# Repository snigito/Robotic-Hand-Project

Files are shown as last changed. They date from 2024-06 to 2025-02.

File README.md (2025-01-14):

# Origin of the project 

The genesis of this independent project was when I was approached by the head of my high school to see if I could make a robotic hand to be “Thing” in our school’s spring musical, the Addams Family. Having a decent knowledge of robotics, computer science and electrical work from working on the robotics team and making other projects, this was an interesting challenge for me. I began to research online and found that there were no commercially made hands and no hands that could be rented. The best robotic hand I saw online was made as a promotion for the Netflix series Wednesday, but it took a professional special effects studio with a team of six people five months to make it. 

After researching different options, I decided to make a robotic hand that would mirror my own hand movements while wearing a glove equipped with sensors. I found someone online who had made an arduino flex-sensor controlled robotic hand. The youtube video I used for inspiration can be found [here](https://www.youtube.com/watch?v=Fvg-v8FPcjg)

# Core Materials

Arduinos are small programmable computers that are cheap and easy to use for small projects like this one. Initially I was using a regular ESP-32, but because they do not have a screen or a battery, it would not have been possible to make Thing wireless. I decided to use the Heltec WiFi LoRa 32 (V3) because it is smaller than a regular Arduino (1” x 0.5”), it has a USB C charging port, a rechargeable battery, WiFi, Bluetooth, and an LED screen. 

<div align="center">
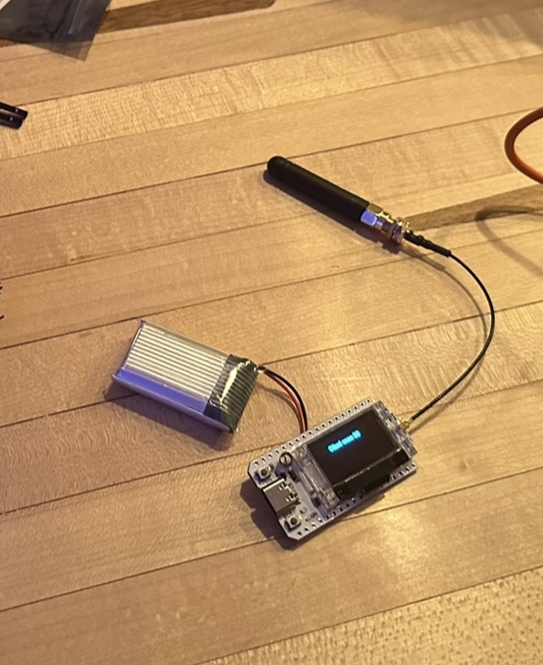
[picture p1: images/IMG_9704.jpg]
Picture of Arduino
  
</div>

The second core component of this project are the flex resistors which are long strips that increase resistance as they are bent. They have little electrical resistance (ohms) when they are straight, but the more they are flexed, the greater the resistance. 

<div align="center">
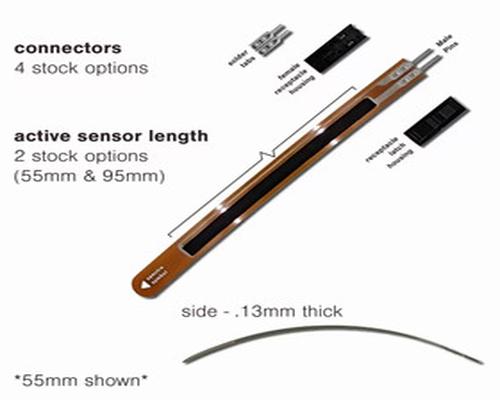
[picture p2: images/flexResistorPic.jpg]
Picture of Flex resistor
  
</div>

The store page to buy these is [here](https://www.spectrasymbol.com/resistive-flex-sensors)

Another important component are the servos, a great staple of any electronics project.

<div align="center">
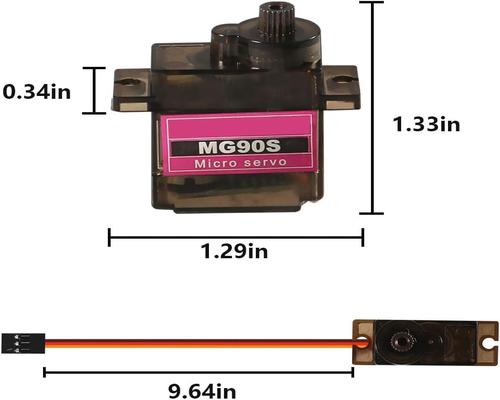
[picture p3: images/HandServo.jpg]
Picture of Servo
  
</div>

These servos can be bought [here](https://tinyurl.com/rhu3s3ph)

The servos I used are very small motors that can turn 180 degrees. I needed them to be small because the idea was that they would fit inside the hand eventually, and I wanted the hand to be a normal size. Servos interface easily with Arduino, and they are easy to code. I used five servos, one for each finger. 

# General Design of the Hand 

The design shown in the above video has a good base, but had a lot of issues I wanted to resolve in my final design. Notably, it used a wired connection meaning that it would not be able to move far from the person controlling it. As a proof of concept this is perfectly fine, but for the play I wanted Thing to be wireless in order to move from one side of the stage to the other seamlessly. To make this possible I planned to use two Arduinos to communicate with each other over WIFI.

To start prototyping the servo movement code with the Arduinos, I got a small robotic hand with servos from amazon. This hand was much too small to use as a final product but it was good to use for testing.  

<div align="center">
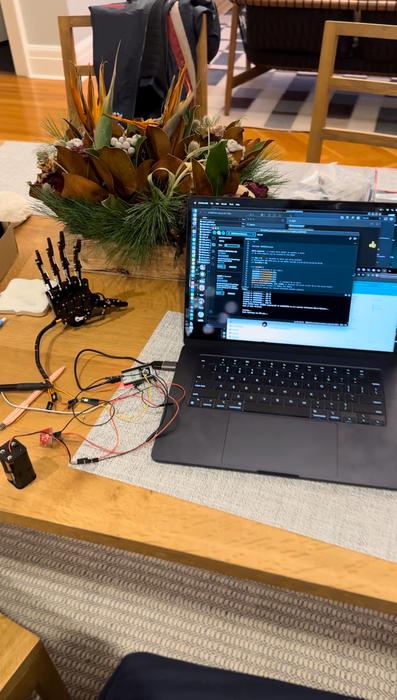
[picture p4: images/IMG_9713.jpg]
Picture of Prototype
  
</div>

Servo motors have a set range of motion (0 to 180). In the code, I put the value that I was setting the servo to in a loop. I started testing the servos by incrementing them and checking both extremes. **VIDEO OF SERVO SWEEP TESTS**

Then I learned about how the WIFI communication system worked between the two Arduinos and repeated the same test. One of the Ardinuos is sending the desired angles to the other one which forwards those commands to the servo and sends it to the desired position. 

Next I made a basic PCB (printed circuit board) so that I could test multiple servos at once in a more streamlined fashion. Each servo needs three wires to function: the power IN (red), the ground which completes the circuit (black), and the signal wire which tells the servo what angle to be at (yellow). In order to make the PCB, I first planned out the routes that I needed the wires to make, counted the pins that I needed going in, and measured the distances of the wires and cut them accordingly. I soldered the wires to the board, made the connections between the (little circles on the board), and used a multimeter to check that each wire was running to where it was supposed to. In the picture below, the top row of pins all go to the servos (5 servos means 15 pins). All of the wires connect to the pins in a sequence: yellow, red, black, yellow, red, black…). In the bottom left, the signal wires go into a ribbon cable connection which connects to the Arduino so that it can control each servo. I had to crimp a female connection onto the ends of the ribbon cable so that it would connect to the male pins on the arduino. The arduino is able to differentiate each servo by the pin number that it is connected to. In the bottom right, the two pins are connected to a small battery pack of AA batteries that provides both the power and ground for the circuit.

<div align="center">
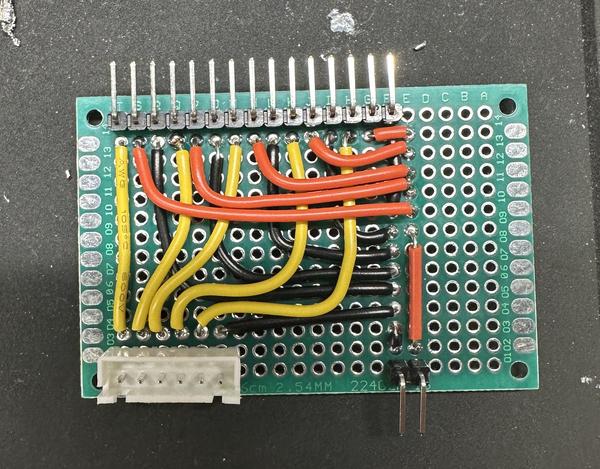
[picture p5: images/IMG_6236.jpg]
Image of Circut Board
  
</div>

<div align="center">
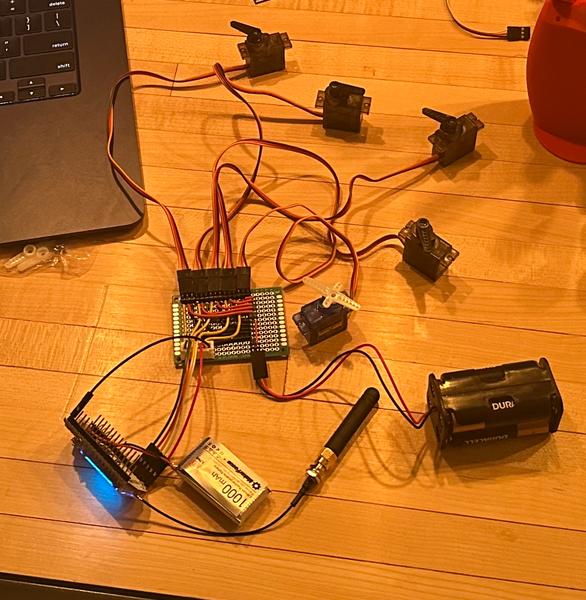
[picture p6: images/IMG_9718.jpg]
Image of Board and Servos
  
</div>

The hand itself and the fingers are all very similar to what was used in the previously mentioned Youtube video. Each finger is separated into three segments (with the thumb being only two segments). Each segment has three holes in it (two of which are larger than the third) and an elastic string is threaded through the holes to hold the fingers together. The elastic string ties off at the tip of each finger and the knuckle at the base of the finger. The elastic string is what is holding the hand together and what keeps the hand upright when the servos are in their “up” position. The tension of the elastic is also what brings the fingers of the hand back up when the servos release to their “up” position. The smaller hole is used for dental floss (fishing line was tried but found to be too stretchy and smooth which resulted in the line detaching from the servos) which connects at the tip of each finger, runs down the inside of the finger through to the palm. The floss is then tied to the servos so that when a servo moves downwards, it will pull on the floss and therefore pull the corresponding finger down. 

<div align="center">
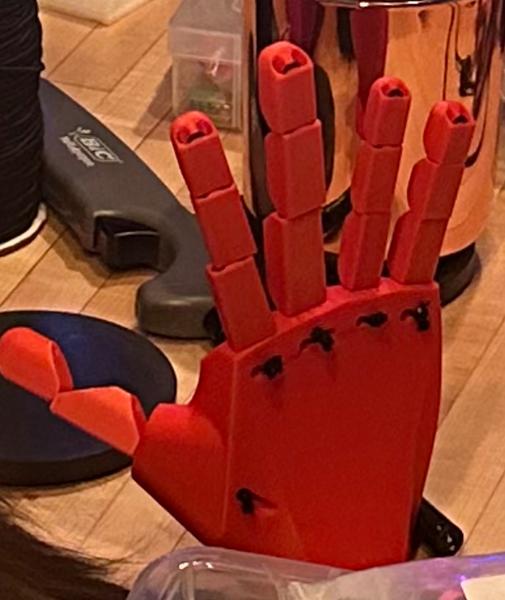
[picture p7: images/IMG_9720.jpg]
Picture of Red Hand 1
  
</div>

<div align="center">
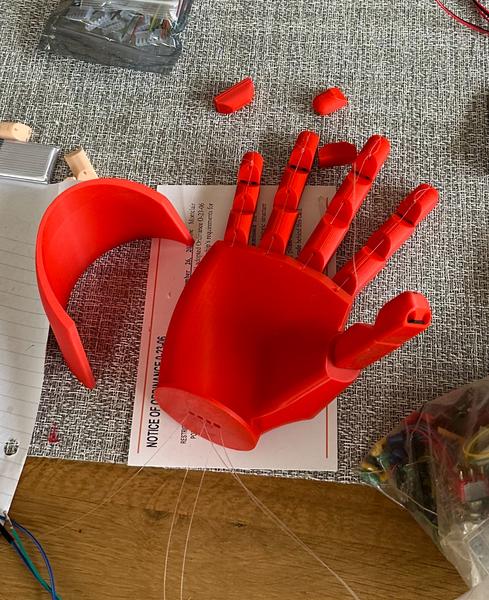
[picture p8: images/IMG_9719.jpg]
Picture of Red Hand 2
  
</div>

These photos show an early prototype 3D printed hand. On the left you see the fishing wire running through and out the bottom of the hand. On the right you can see the black elastic string running through and tied off at the base of the fingers.

The next steps were to figure out a way to mount the servos inside the wrist portion of the hand. The servos needed to fit in a way where their movement arcs would not intersect with one another. In the video I used for inspiration the person doing the project decided to glue the servos to the 3D print but I did not like the idea of that so I decided to make something more permanent. I used metal inserts that can be pressed into the 3D print which allowed me to screw the servos down. I used a special tip for the hot soldering iron to melt the plastic and press the insert into it.

<div align="center">
  Image of First Hand Servo Layout
</div>

<div align="center">
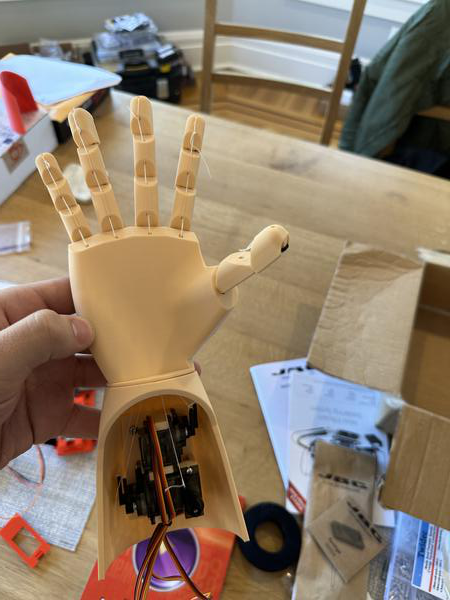
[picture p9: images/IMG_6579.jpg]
Image of Final Hand Servo layout
  
</div>

I changed over to a skin tone color for the 3D print. On the left is an initial servo layout that I tested, but ultimately decided that it did not fit well. 

In order to make the Arduino, circuit board, servo motors, and batteries fit inside the casing I made a new circuit board and changed the layout of the battery pack. The new circuit board had connections so that the Arduino could plug in to the board directly with no wires in between. The battery pack I changed to a flat one where 4 AA batteries are laid parallel to one another and then recessed into the bottom of the housing. This allows for easy access to change out the batteries, adds weight to the bottom to prevent tipping, and is compact so it does not get in the way of other parts. Additionally, there is a small, rechargeable LIPO battery that powers the arduino. The larger battery pack powers the servos in conjunction with the smaller one to make the system work. For ease of use I also added a switch for the power battery wires. It is a DPDT switch with one throw wired in to cut off or allow the flow of power without having to take off the casing to turn it on. I also added a thumbscrew to the casing with a threaded insert to easily access the interior of the hand. I implemented a similar design with the back plate that the servos screw into so that the whole layout could be removed for easy access and servicing. 

<div align="center">
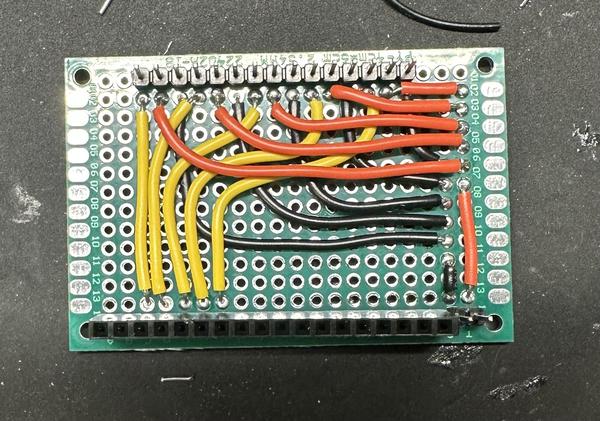
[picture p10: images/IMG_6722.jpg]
Circut Board Picture
  
</div>

<div align="center">
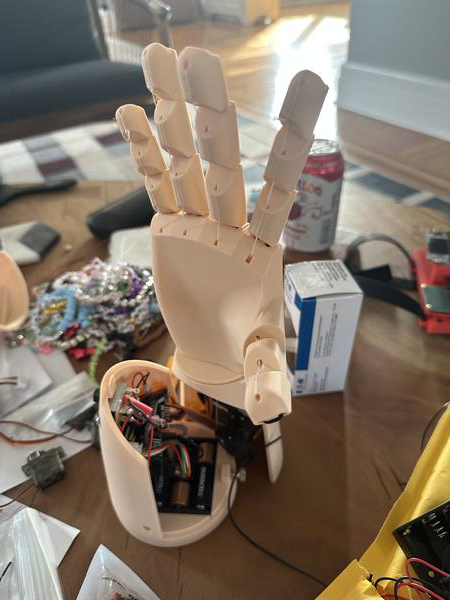
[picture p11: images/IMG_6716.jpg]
Picture of Hand Assembly
  
</div>

The new board shown on the left is functionally the same as the previous one but without the ribbon cable connection so as to cut down on space. The image on the right shows the recessed battery pack, silver thumb screw on the left and the power switch on the top left above the Arduino.

The ranges of the values of the flex resistors were too large  so I used a voltage divider to help balance it out. The signal wires are reading from the voltage after the resistor. 

<div align="center">
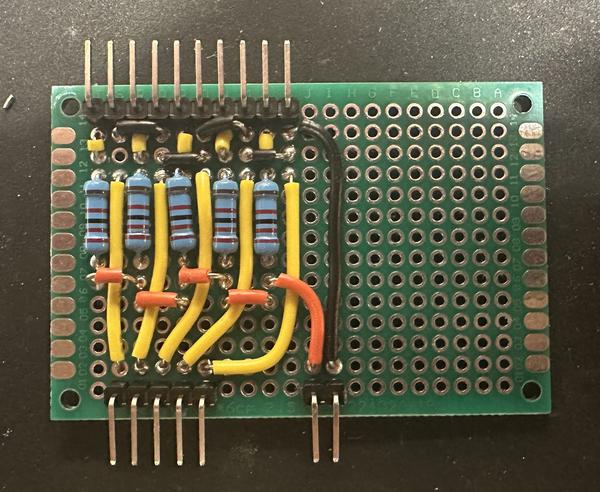
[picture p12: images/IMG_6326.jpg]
Voltage Divider Circut Picture
  
</div>

I designed an arm piece that would strap to my arm using velcro and would hold an arduino and a battery. It could then read the resistance values from each flex resistor and then send it to the other arduino inside the hand. The arduino in the hand then uses these values to move the servos and make the fingers match how mine are moving in the glove. 

<div align="center">
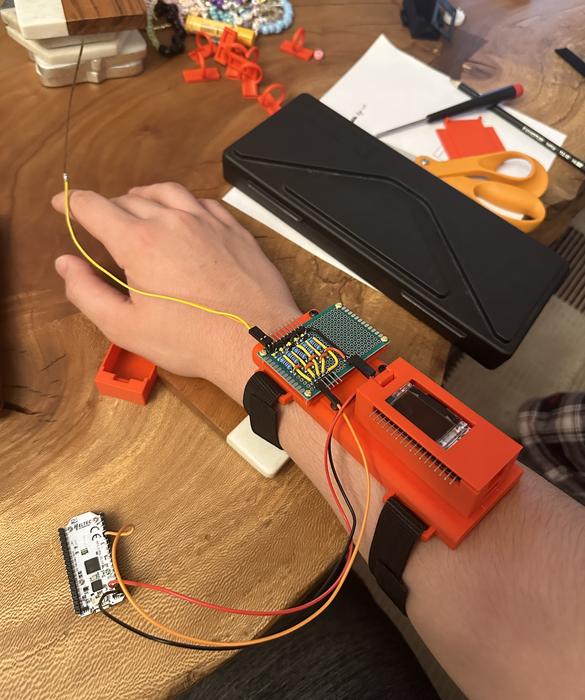
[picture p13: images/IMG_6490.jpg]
Arm Piece Picture
  
</div>

I bought an outdoor work glove and 3D printed guide rails for the flex resistors so that they would stay in a uniform position on each of my fingers. I sewed these guide rails into the outdoor work glove. I also sewed the base of each flex resistor to the base of each finger on the glove. After a few days of play rehearsals which was heavy testing for the glove and the hand, I noticed that the flex resistors values would no longer reflect the originals that we set. I had to hold my fingers and the resistors at awkward angles just to get to the original positions. Sometimes, even that would not work. After some research online, it became clear to me that the resistors’ degradation was a known problem. Therefore, I decided to make a new glove, and on this new one I would sew down the base of each resistor much more than I had on the first glove. 

<div align="center">
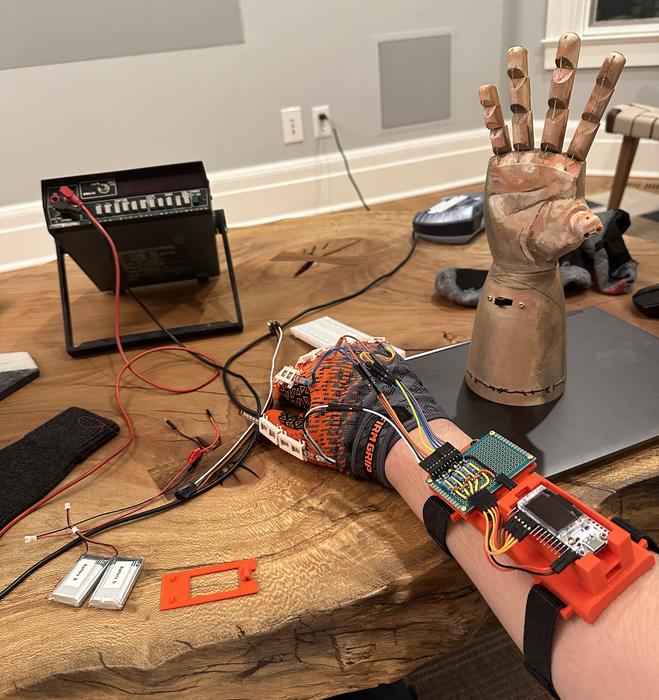
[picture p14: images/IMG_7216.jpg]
Full Glove Picture
  
</div>

All of the programming files can be found below and are fully commented. When running the hand, first I plugged in the battery for the glove arduino, and it starts to look for a specific WIFI network with a specific name and would try the password that we gave it. The Arduino in the hand acts as a WIFI network and the one in the glove works as a WIFI client. This allows the two devices to communicate and send messages to one another. In this case I am using the glove Arduino to record the values of the flex resistors then scale those values to a number between 0 and 180 relative to the resistor’s minimum and maximum. The glove Ardunio then takes that number and the resistor number and sends the hand Ardunio a message in this format: “[resistor number] [desired angle]”. The resistor number corresponds to the servo controlling the same finger which the hand Ardunio sets to the desired angle after receiving the message. Both Arduinos display the values and the resistor number on their OLED screens in a scrolling format. The next value is displayed at the bottom and the preceding ones are shifted up to help with debugging to ensure all the values are expected as well as all the resistors are responsive. The code for this can be found in the text scrolls file. The code for the hand can be found in the 5 servo access point file. The code for the glove is found in the 5 servo client file.

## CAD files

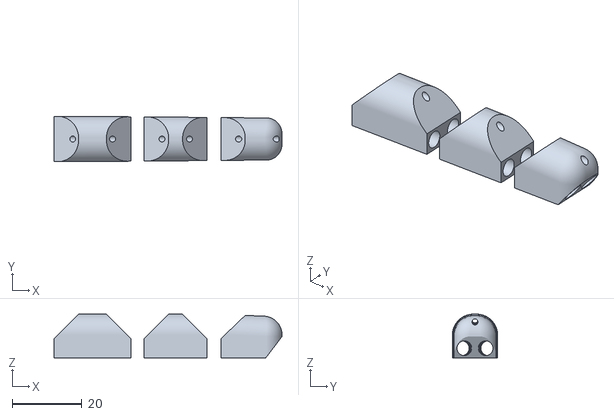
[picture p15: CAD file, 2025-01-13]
Hand Parts/finger_pinky.stl
65.2 x 13.0 x 12.5

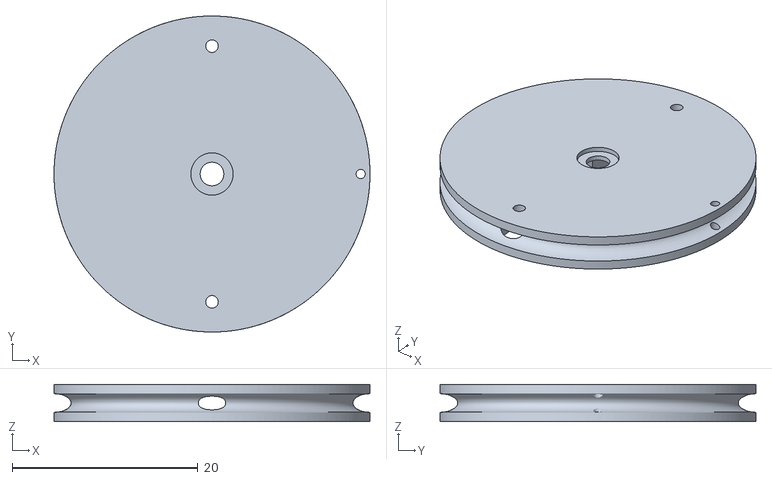
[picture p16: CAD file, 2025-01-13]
Hand Parts/large_servo_horn.stl
34.0 x 34.0 x 4.00

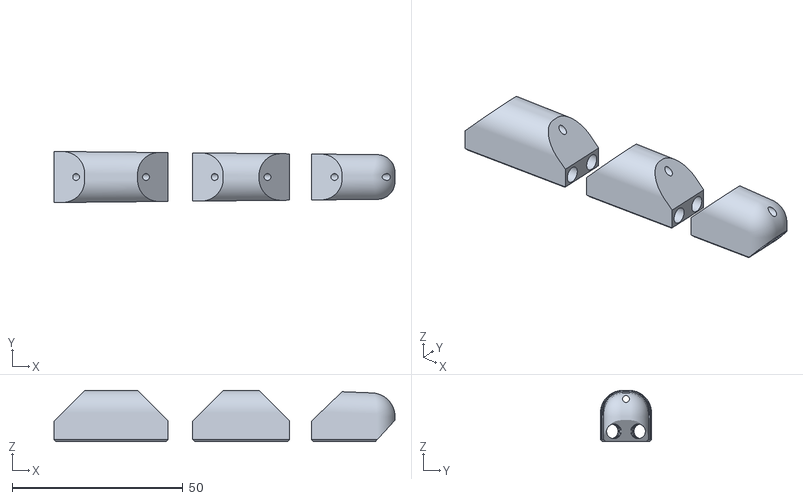
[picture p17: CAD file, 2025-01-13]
Hand Parts/finger_middle.stl
100.0 x 15.0 x 15.0

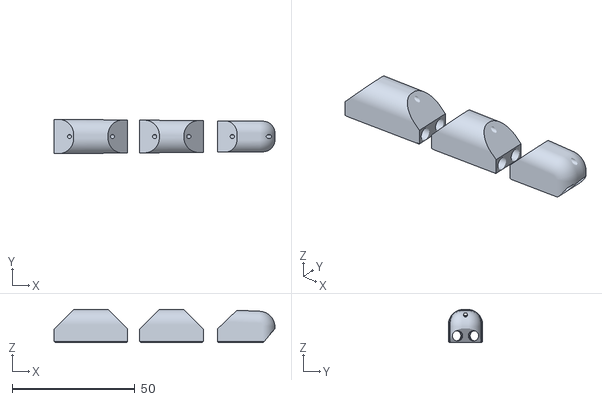
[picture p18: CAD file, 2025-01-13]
Hand Parts/finger_ring.stl
90.0 x 14.0 x 13.5

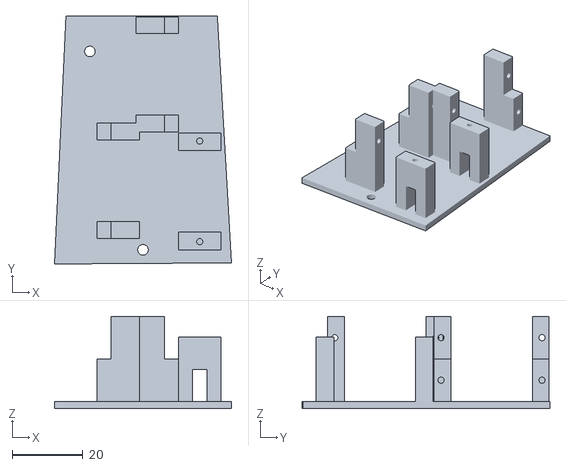
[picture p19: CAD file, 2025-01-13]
Hand Parts/stacked_servo_mount.stl
50.0 x 70.0 x 26.0

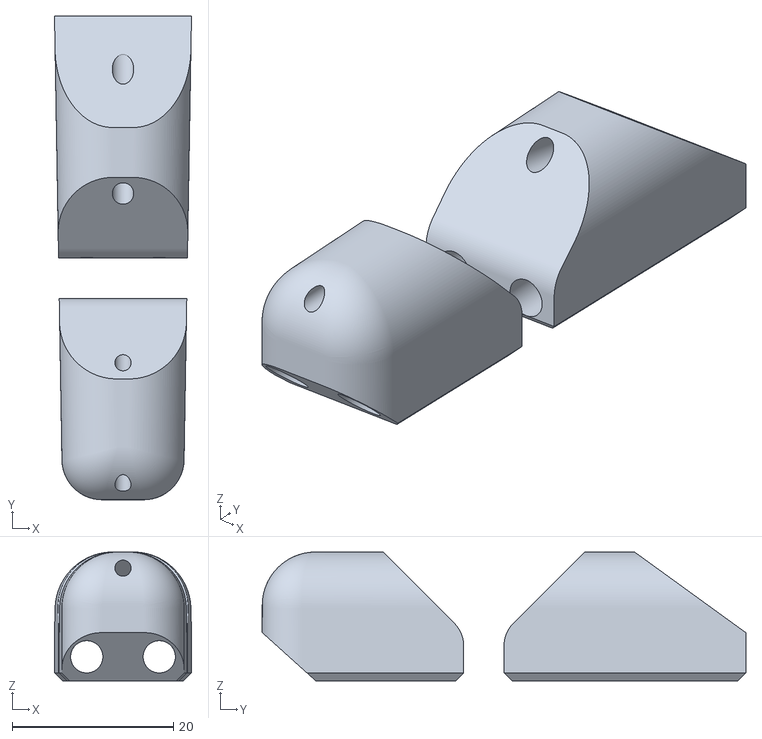
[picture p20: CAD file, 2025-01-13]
Hand Parts/finger_thumb.stl
17.0 x 60.0 x 16.0

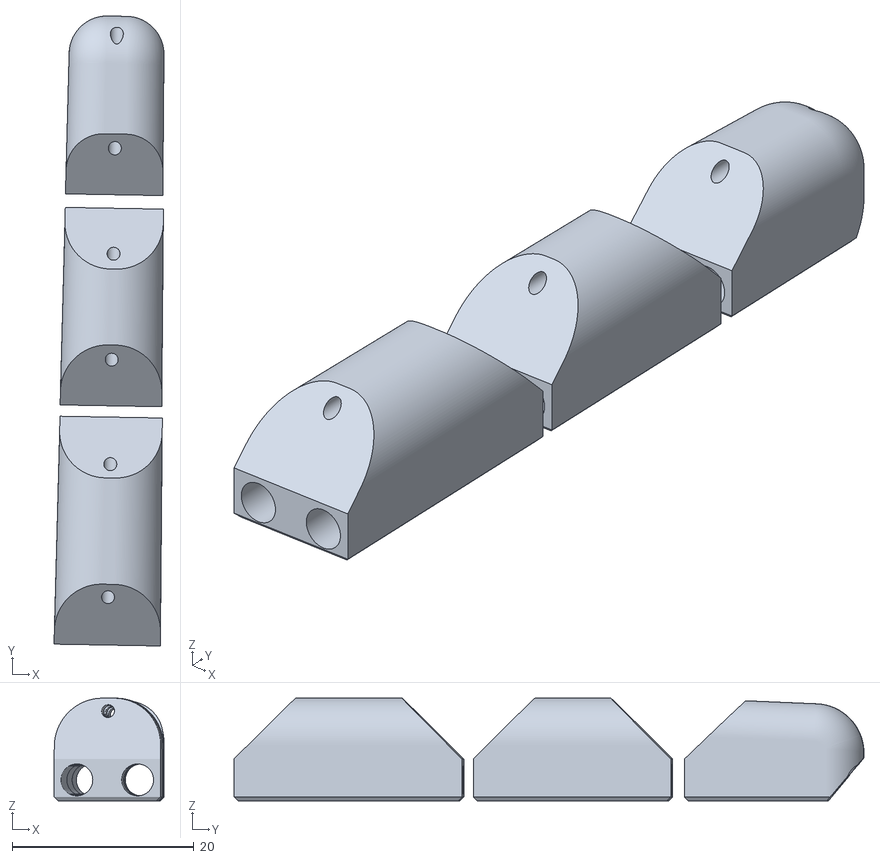
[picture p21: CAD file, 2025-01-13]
Hand Parts/finger_index.stl
12.1 x 69.4 x 11.3

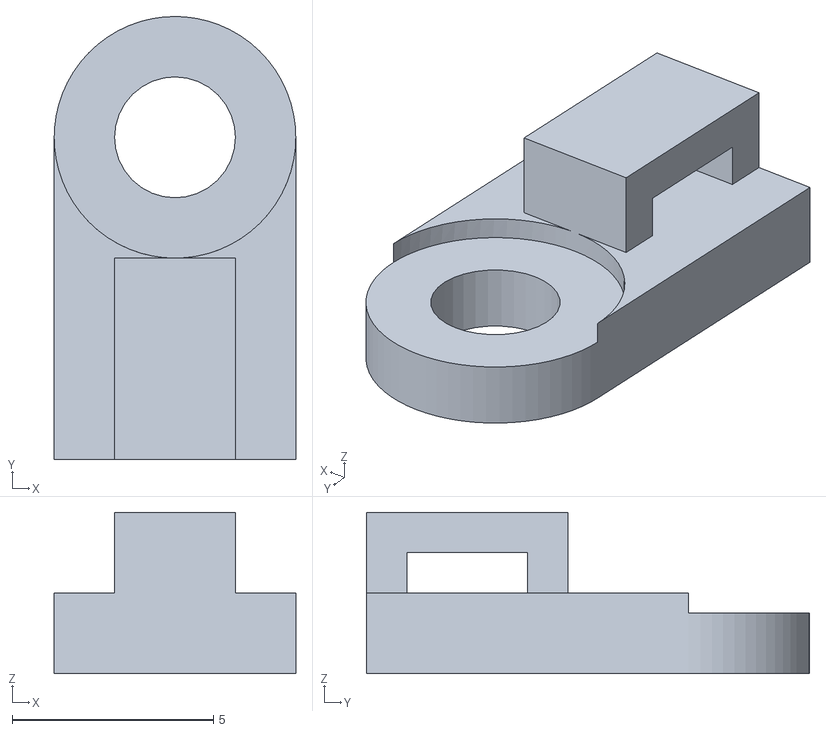
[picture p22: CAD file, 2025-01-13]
Hand Parts/wire_holder.stl
6.00 x 11.0 x 4.00

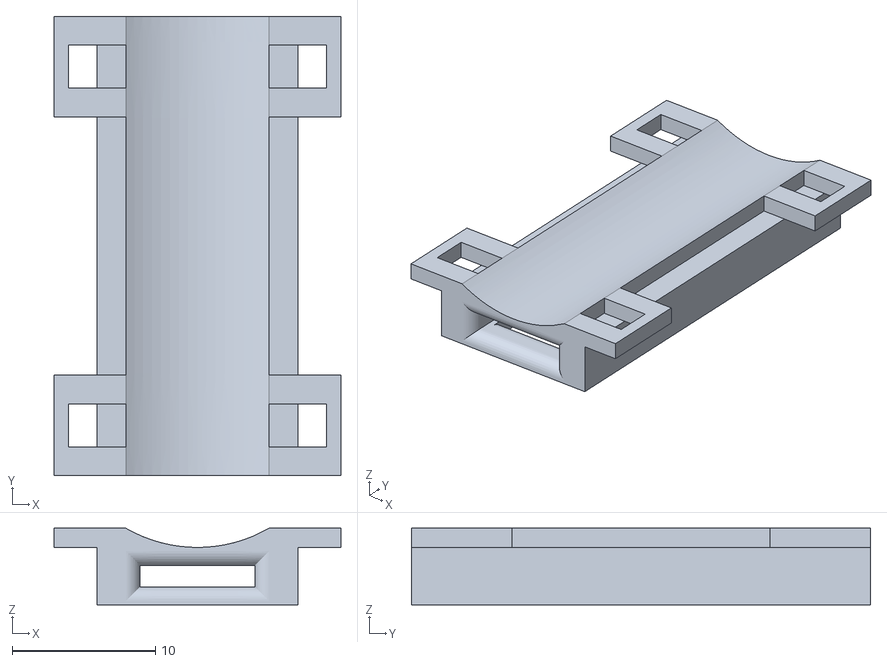
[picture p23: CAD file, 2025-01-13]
Hand Parts/glove_sensor_glides.stl
20.0 x 32.0 x 5.34

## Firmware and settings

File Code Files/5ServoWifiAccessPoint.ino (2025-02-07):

/*
  WiFiAccessPoint.ino creates a WiFi access point and provides a web server on it.

  Steps:
  1. Connect to the access point "yourAp"
  2. Point your web browser to http://192.168.4.1/H to turn the LED on or http://192.168.4.1/L to turn it off
     OR
     Run raw TCP "GET /H" and "GET /L" on PuTTY terminal with 192.168.4.1 as IP address and 80 as port

  Created for arduino-esp32 on 04 July, 2018
  by Elochukwu Ifediora (fedy0)
*/
#define WIFI_LoRa_32
#include "heltec.h"
#include "text_scrolls.h"
#include <WiFi.h>
#include <WiFiClient.h>
#include <WiFiAP.h>
//#include <ESP32Servo.h>
#include <pwmWrite.h>

// Set these to your desired credentials.
const char *ssid = "mustang2";
const char *password = "password";

// for the ESP32-S3 the GPIO pins are 1-21,35-45,47-48

Pwm pwm = Pwm();

int servoPins[5] = {5,4,3,2,1};

WiFiServer server(80);

void setup() {
  Serial.begin(115200);
  Heltec.begin(true /*DisplayEnable Enable*/, false /*LoRa Enable*/, true /*Serial Enable*/);
  Heltec.display->setTextAlignment(TEXT_ALIGN_LEFT);
  Heltec.display->setFont(ArialMT_Plain_10);
  print("Configuring access point...");
  delay(2000);

  // You can remove the password parameter if you want the AP to be open.
  // a valid password must have more than 7 characters
  if (!WiFi.softAP(ssid, password)) {
    print("Soft AP creation failed.");
    while(1);
  }
  IPAddress myIP = WiFi.softAPIP();
  print("AP IP address: ");
  print(myIP.toString());
  server.begin();
  delay(1000);
  clearBuffer();
  print("Server Started");
  delay(1000);
}

void debugPrint(String& line, int angle, int servoNum) {
  char buf[256];
  sprintf(buf, "Servo%d angle [%s] = [%d]", servoNum, line.c_str(), angle);
  print(buf);
}

void loop() {
  WiFiClient client = server.available();   // listen for incoming clients

  if (client) {                             // if you get a client,
    print("New Client.");           // print a message out the serial port
    String currentLine = "";                // make a String to hold incoming data from the client
    while (client.connected()) {            // loop while the client's connected
      while (client.available() && client.connected()) {
        char c = char(client.read());             // read a byte, then
        if (c == '\n')                    // if the byte is a newline character
          break;
        else if (c != '\r')  // if you got anything else but a carriage return character,
          currentLine += c;  // add it to the end of the currentLine
      }
      if (currentLine.length() > 0) {
        int servoNumber = (int)currentLine.charAt(0) - (int)'0';
        int angle = atoi(currentLine.substring(2).c_str());
        debugPrint(currentLine, angle, servoNumber);
        pwm.writeServo(servoPins[servoNumber], angle);
        currentLine.clear();
      }
    }
    // close the connection:
    client.stop();
    print("Client Disconnected.");
  }
}

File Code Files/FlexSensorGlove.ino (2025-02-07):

#include <WiFi.h>
#include "heltec.h"
#include "text_scrolls.h"
#include <WiFiClient.h>
#include <WiFiAP.h>

const char* ssid = "mustang2";      // Change this to your WiFi SSID
const char* password = "password";  // Change this to your WiFi password

// Recommended PWM GPIO pins on the ESP32 include 2,4,12-19,21-23,25-27,32-33
int ADC_Max = 4096;  // This is the default ADC max value on the ESP32 (12 bit ADC width);
                     // this width can be set (in low-level oode) from 9-12 bits, for a
                     // a range of max values of 512-4096
//refrence nums: int flex_Min = 2048; int flex_Max = 2600;

int flex_Min = 1000;
int flex_Max = 2300;

int sensors[5] = { 5, 4, 3, 2, 1 };
int vals[5] = { 0, 0, 0, 0, 0 };
int rawVals[5] = { 0, 0, 0, 0, 0 };
int prevVals[5] = { 0, 0, 0, 0, 0 };
int minRaw[5] = { 1102, 1416, 1186, 1191, 1317 };  //1215, 1227, 1259, 1481, 2227
int maxRaw[5] = { 2643, 3001, 2239, 2745, 2613 };  //2650, 2437, 2515, 2698, 4095

void setup() {
  Serial.begin(115200);
  Heltec.begin(true /*DisplayEnable Enable*/, false /*LoRa Enable*/, true /*Serial Enable*/);
  Heltec.display->setTextAlignment(TEXT_ALIGN_LEFT);
  Heltec.display->setFont(ArialMT_Plain_10);
  for (int i = 0; i < 5; i++) {
    vals[i] = rawVals[i] = 0;
    prevVals[i] = -11;
  }

  print("Done with set up");
}

void debugPrint(int sensorNum, int reading) {
  char buf[256];
  sprintf(buf, "Snr %d reading = [%d]", sensorNum, reading);
  print(buf);
}

void rawDebugPrint(int sensorNum, int rawReading) {
  char buf[256];
  sprintf(buf, "Snr %d RawRead = [%d]", sensorNum, rawReading);
  print(buf);
}

void minMaxDebugPrint(int sensorNum, int min, int max) {
  char buf[256];
  sprintf(buf, "Snr%d Min[%d] Max[%d]", sensorNum, min, max);
  print(buf);
}

long ourMap(long x, long in_min, long in_max, long out_min, long out_max) {
  const long run = in_max - in_min;
  if (run == 0) {
    log_e("ourMap(): Invalid input range, min == max");
    return -1;  // AVR returns -1, SAM returns 0
  }
  const long rise = out_max - out_min;
  const long delta = x - in_min;
  long result = (delta * rise) / run + out_min;
  result = min(out_max, result);
  result = max(out_min, result);
  return result;
}

int minRawSeen[5] = { 4096, 4096, 4096, 4096, 4096 };  //1215, 1227, 1259, 1481, 2227
int maxRawSeen[5] = { 0, 0, 0, 0, 0 };                 //2650, 2437, 2515, 2698, 4095

void minMaxDebugPrint() {
  char buf[256];
  Heltec.display->clear();
  for (int i = 0; i < 5; ++i) {
    sprintf(buf, "%d: %d,%d [%d]", i, minRawSeen[i], maxRawSeen[i], vals[i]);
    Heltec.display->drawString(0, i * 10, buf);
  }
  Heltec.display->display();
}

void loop() {
  for (int i = 0; i < 5; i++) {
    vals[i] = rawVals[i] = analogRead(sensors[i]);
    vals[i] = ourMap(vals[i], minRaw[i], maxRaw[i], 0, 180);  // scale it to use it with the servo (value between 0 and 180)

    minRawSeen[i] = (rawVals[i] < minRawSeen[i]) ? rawVals[i] : minRawSeen[i];
    maxRawSeen[i] = (rawVals[i] > maxRawSeen[i]) ? rawVals[i] : maxRawSeen[i];
  }

  for (int i = 0; i < 5; i++) {
    if (i == 0 || i == 1) {  // i is reffring to the servo number
      vals[i] = 180 - vals[i];
    }
    if (vals[i] >= (prevVals[i] + 10) || vals[i] <= (prevVals[i] - 10)) {
      prevVals[i] = vals[i];
      // debugPrint(i, vals[i]);
    }
  }

  delay(100);
  minMaxDebugPrint();
}
